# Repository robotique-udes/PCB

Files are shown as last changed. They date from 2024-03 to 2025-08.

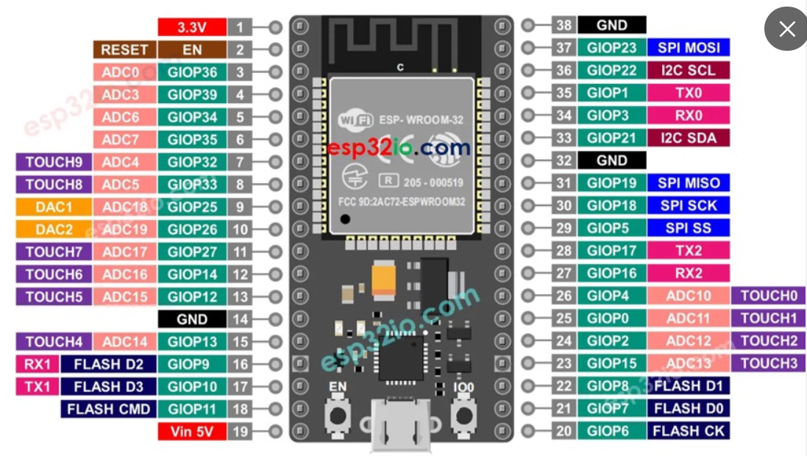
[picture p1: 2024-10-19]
exo/ACE 2024/Motherboard/ESP32_CHUNGUS_RAPIDUS/Pinout_ESP32.png

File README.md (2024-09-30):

# PCB

Cette repo regroupe les fichiers et projets de PCB de tous les sous-groupe de robotique UdeS. Chaque groupe s'organise dans son dossier. Dans le futur il serait pertinent de monter une librairie de Symbole et de Footprint globale entre les groupes.

## Protection de branches:

- Seulement les branches nommées avec ce pattern sont acceptées:
  - rover/**
  - exo/**

- Une Pull Request est requise pour pouvoir merge dans le main

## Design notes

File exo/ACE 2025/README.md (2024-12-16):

# 2025 Standard électronique
Pour la fixation des pcb, il est standardisé d'utiliser des vis M3.
Ne pas utiliser de micro vias.
## PIN Layout pour la communication en cable ethernet
Pin 1: CAN+
Pin 2: CAN-
Pin 3: SCL+
Pin 4: SCL-
Pin 5: SDA+
Pin 6: SDA-
Pin 7: 5V
Pin 8: GND

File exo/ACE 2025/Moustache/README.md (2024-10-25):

# 2025 Exo Moustache 
The Moustache is a small pcb made to receive I2C in differential, CAN and power by an ethernet port and distributed trought 6 other ethernet port to connect the captors and motors.
## PIN Layout
Pin 1: CAN+

Pin 2: CAN-

Pin 3: SCL+

Pin 4: SCL-

Pin 5: SDA+

Pin 6: SDA-

Pin 7: 5V

Pin 8: GND
## Port Layout
MOTG = moteur Genou

MOTH = moteur Hanche

BNOF = BNO Femur

BNOT = BNO Tibia

EXT = extra

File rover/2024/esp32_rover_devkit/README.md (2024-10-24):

# Antenna
PCB servant de module GPS

Voici les informations concernant le PCB : Module GPS

## Image du PCB en 3D
Capture d’écran, le 2024-09-25 à 21 09 17

## Objectifs:
* Permettre au Rover d'avoir des information sur sa position GPS

## Composants principaux:
* ESP32-S3-WROOM-1
* TJA1050T (CAN BUS)
* BN-880 (GPS)
* Ports Ethernets
* AZ1117ID-3.3 (LDO)
* TVS diodes

## Fonctionnement:
Le MCU peut lire les données du GPS.
Le MCU peut transmettre les informations du GPS par le CAN bus.
Le CAN bus peut passer à travers le circuit, donc un autre circuit peut être branché à la suite de celui-ci.

## PGIO
### Outputs

Name         | GPIO
---          | ---
LED_BUILDIN  | D2
STEPPIN      | D37
DIRPIN       | D38
ENABLEPIN    | D39

### Communication

Name    | GPIO
---     | ---
USBN    | D19
USBP    | D20
SCL     | D21
SDA     | D09
TX_GPS  s| D13
RX_GPS  | D12
TXC     | D48
RXC     | D47

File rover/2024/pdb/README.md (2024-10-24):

# PDB (Power Distribution Board)
PCB servant à gérer la distribution à bas courant et le de data du rover

## Image du PCB en 3D
Capture d’écran, le 2024-09-18 à 21 24 36

## Objectifs:
* Protéger tous les autres boards du Over/Under Voltage pour le 5V, 12V et 24V
  * Seulement le 5v et le 24v sont protégé, car les résistance 5% ont trop  d'incertitude.
* Injecteur POE(12V custom pinout) pour les cameras branché en Ethernet
  * On/Off possible par le MCU
* Diriger le signal des cameras sur les bonnes pins selon la norme Ethernet
* Agir en tant que POE pour les antennes 24V (vrai POE)
* Controller l'alimentation de 2 circuit d'accessoires 12V 
  * Par 2 connecteurs Ethernet
* Permettre de pouvoir sortir une des 3 tension (5v, 12v, 24v) par un screw terminal
  * Alimente la switch ethernet en dessous
* MCU Connecté sur le CAN BUS
* Sélectionner avec les GPIO les cameras qui doivent recevoir du power

## Composants principaux:
* ESP32 DEV KIT V1
* TJA1050 (CAN BUS)
* LTC4365 (Over/Under Voltage protaction)
* DMG4822SSD (DIODE pour la switch du LTC4365)
* DELs
* CLP6C-FKB-CKNPRGJBB7A363 (ERROR DEL)
* Boutons
* Horizontal Amphenol 54602 RJ45
* ASSMANN_A-2014 Ethernet connector
* CRJ036-5-TH_2x4 Ethernet connector
* BTS5200 (4 Channel Mosfet)

## Fonctionnement:
- Le PDB reçoit 3 tensions régulé en entrée, du 5V, du 12V et du 24V.
- Le 12V sert principalement pour alimenter les caméras qui sont alimentés avec un POE avec un Pinout spécial. Il sert aussi à alimenter 2 circuit d'accessoires potentiels.
- Le 24V sert à alimenter le/les antennes qui sont sur le Rover.
- Le 5V est passé avec les fils de CanBus pour alimenter et communiquer avec les autres PCB du rover
- Le circuit sécurise les trois tensions contre les sur-tensions et le drops de tensions.
- La sortie vers l'ordinateur principal n'est pas utilisé, l'ordinateur est directement branché dans la switch.

## PGIO
### Outputs

| Name | GPIO |
|---|---|
| CAM_SIGN_0 | D18  |
| CAM_SIGN_1 | D19  |
| CAM_SIGN_2 | D33  |
| CAM_SIGN_3 | D32  |
| PWM_0 | D21  |
| PWM_1 | D22  |
| ACC1_CONTROL | D23  |
| ACC2_CONTROL | D25  |
| LED_R | D14  |
| LED_G | D27  |
| LED_B | D26  |

### Communication

| Name | GPIO |
|---|---|
| TXC  | D6 |
| RXC  | D7 |

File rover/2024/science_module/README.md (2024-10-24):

# PCB du module science

## Image du PCB en 3D
Capture d’écran 2024-10-02 202944

## Objectifs:
* Contrôller les actionneurs du module science
  * Fan
  * Moteur DC (Grinder)
  * Actuateur linéaire
  * 4x servos
* PDB pour ces actionneurs
* Communication avec le reste du Rover

## Composants principaux:
* ESP32 S3 WROOM
* Connecteur Ethernet
* 2x bouton
* Connecteur XT60 mâle
* 6x connecteur XT30 femelle
* 2x connecteur XT30 mâle
* 8x connecteur à 2 pins
* Connecteur à 4 pins
* 6x slot à fusible
* LED

## Fonctionnement:
* Le PCB reçoit du 24V par le XT60
* Un buck down 24V -> 5V externe est connecté par deux XT30 (1 femelle, 1 mâle)
* Un buck down 24V -> 12V externe est connecté par deux XT30 (1 femelle, 1 mâle)
* Chacune des deux fans du vaccum a un connecteur XT30 à 12V
* Le grinder et l'actuateur linéaire sont chacun alimentés par un connecteurs XT30 à 24V
* LIN_IN_1 et LIN_IN_2 passent par un H-bridge et deviennet LIN+ et LIN- afin de pouvoir contrôller le sens de l'actuateur linéaire
* Les 8 connecteurs à 2 pins servent à ??????????? (Envoyer des signaux de contrôle? PB?)
* La pin 1 du ethernet est le CAN High et la pin 2 est le CAN Low

## PGIO:
### Outputs

| Name | GPIO |Commentaires |
|---|---|---|
| GRINDER_PWM  | IO10 | |
| PB_GRINDER | IO11 | |PB -> outputs ou inputs? PB-> Push Button? Connecteurs?
| FAN_B_PWM | IO3  | |
| FAN_A_PWM | IO9  | |
| PB_VACCUM | IO38 | |
| Servo_0 | IO7  | |
| Servo_1 | IO15 | |
| Servo_2 | IO16 | |
| Servo_3 | IO17 | |
| LIN_IN_1 | IO18 | Parle au H-Bridge |Outputs pour l'actuateur linéaire?
| LIN_IN_2 | IO8  | Parle au H-Bridge |
| PB_UP | IO14 | |
| PB_DOWN | IO21 | |
| PB_CAROUSSEL | IO12 | |
| PB_SPARE | IO13 | |
| LED_BUILDIN  | IO5  | |À quoi sert cette LED?

### Inputs

| Name | GPIO |Commentaires |
|---|---|---|
| EN_PB | EN | Bouton Enable |
| GPIO_0 | IO1  | Bouton Boot |
| LS_EXT | IO2  | Limit switch |
| LS_RET | IO3  | Limit switch |

### Communication

| Name | GPIO |Commentaires |
|---|---|---|
| RXC | IO47 | Parle au Ethernet (CanBus) |
| TXC | IO48 | Parle au Ethernet (CanBus) |
| USB_N | IO19 | Parle au port micro-SD |
| USB_P | IO20 | Parle au port micro-SD |

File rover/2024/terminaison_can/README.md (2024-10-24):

# Terminaison CAN bus
Petit PCB qui sert de terminaison aux extrémités du CAN bus.

## Image du PCB en 3D
Capture d’écran, le 2024-09-25 à 19 42 32

## Objectifs:
* Requis de la couche transport du CanBus:
  * 2 terminaisons de 120 ohms doivent être branchés aux extrémités du bus.
    * Sur un bus OK on doit mesurer 60 Ohms
* Agir comme un indicateur visuel de s'il y a de l'alimentation en parallèle des lignes CanBus

## Composants principaux:
* Connecteur RJ45 pour câble ethernet
* 2x Résistances 60 ohms
* Condensateur 47nF
* Résistance 2k ohms
* DEL

## Fonctionnement:
Deux résistances de 60 ohms sont placées en série entre le CAN HIGH et le CAN LOW en une résistance combinée de 120 ohms, ce qui est le standard dans une terminaison CAN. La résistance permet de dissiper le signal passant dans le bus.

Le condensateur permet de créer un filtre passe-bas qui nettoie encore plus le signal.

Il y a aussi une résistance et une diode qui sont connectées entre le VCC et le GND afin d'indiquer visuellement (par une DEL allumée) qu'il y a du courant sur les pins 7 et 8.

## Références:
* https://electronics.stackexchange.com/questions/512653/can-split-termination-capacitor-calculation
* https://www.mouser.ca/datasheet/2/302/TJA1050-3083416.pdf

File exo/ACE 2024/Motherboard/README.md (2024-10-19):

# Motherboard
Mise à jour 2024 avec un mutliplexeur embarqué pour la communication avec les 5 BNO_085. Le board est supposé être utilisé avec un ESP-WROOM-32.

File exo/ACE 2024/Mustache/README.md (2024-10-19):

# Mustache breakout board
PCB présent sur chaque jambe pour la redistribution des signaux I2C et des encodeurs. Les connecteurs sont des MOLEX disponibles dans le dossier Bibliotheque.

## Problèmes connus
- L'ajout d'une résistance pull-up avec le 3v3 à été nécessaire pour aider l'intégrité du signal I2C

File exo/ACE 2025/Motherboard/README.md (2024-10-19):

# 2025 Exo Motherboard
PCB principal sur l'exo, utilisant le SoM en socket M2 ayant un ESP-32-S3.

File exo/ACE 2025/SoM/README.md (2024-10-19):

# SoM
ESP32-S3 on a compact format with a M2 socket connecter for integration on other board.

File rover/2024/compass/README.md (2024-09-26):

# Antenna
PCB servant de module de centrale inertielle et de boussole

Voici les informations concernant le PCB : Module Compass

## Image du PCB en 3D
Capture d’écran, le 2024-09-25 à 20 08 11

## Objectifs:
* Permettre au Rover d'avoir des information sur sa position et son orientation dans l'espace
* 

## Composants principaux:
* ESP32-S3-WROOM-1
* TJA1050T (CAN BUS)
* WT901 (compass)
* Ports Ethernets
* AZ1117ID-3.3 (LDO)
* TVS diodes

## Fonctionnement:
Le MCU peut lire les données de la centrale inertielle et boussole par UART.
Le MCU peut transmettre les informations du senseur par le CAN bus.
Le CAN bus peut passer à travers le circuit, donc un autre circuit peut être branché à la suite de celui-ci.

## PGIO
### Outputs

Name         | GPIO
---          | ---
LED_BUILDIN  | D2
STEPPIN      | D37
DIRPIN       | D38
ENABLEPIN    | D39

### Communication

Name    | GPIO
---     | ---
USBN    | D19
USBP    | D20
SCL     | D21
SDA     | D09
TX_WT   | D13
RX_WT   | D12
TXC     | D48
RXC     | D47

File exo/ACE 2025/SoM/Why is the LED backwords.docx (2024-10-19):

Why is the LED backwords? It is fixed

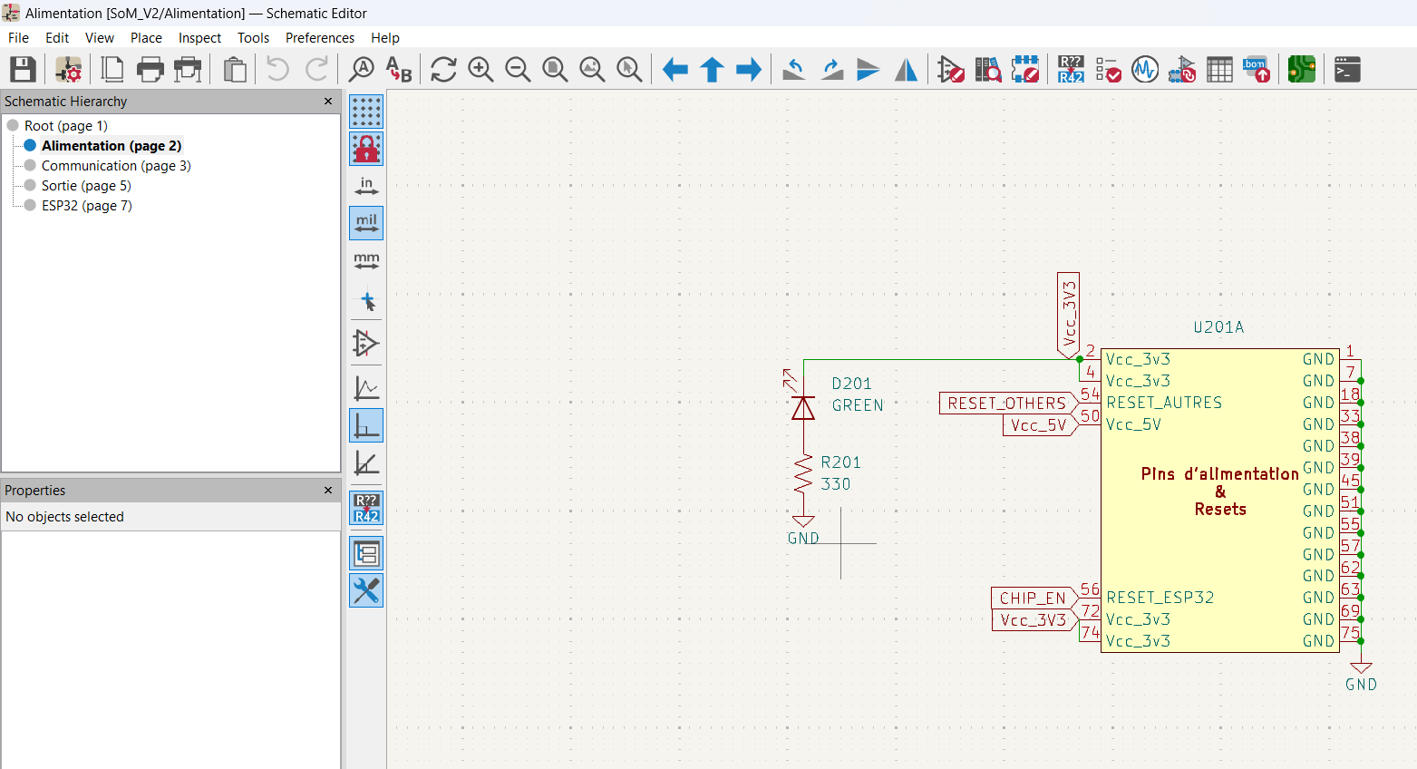
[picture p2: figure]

GND a la patte 3? Non, c Frank qui est cave, c sure que c pas un GND.

Mais le CAP(C303) me pose question? C fine

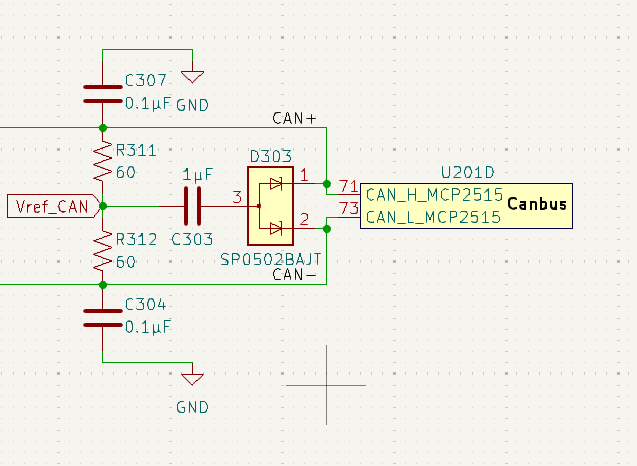
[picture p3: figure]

Will have to make sure? Should be fine

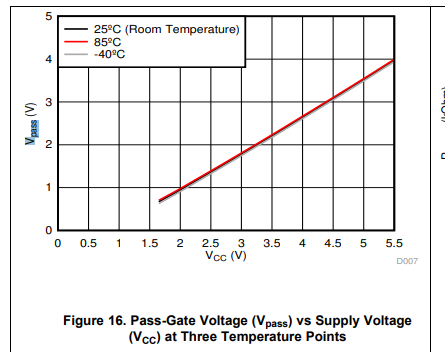
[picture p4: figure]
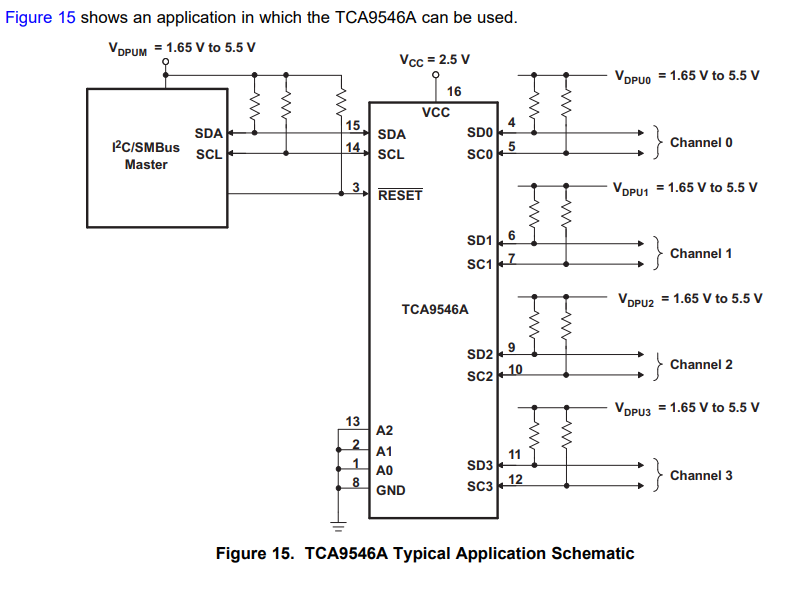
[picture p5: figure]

DS_FT231

Weird thing happening on pin 10 and 12

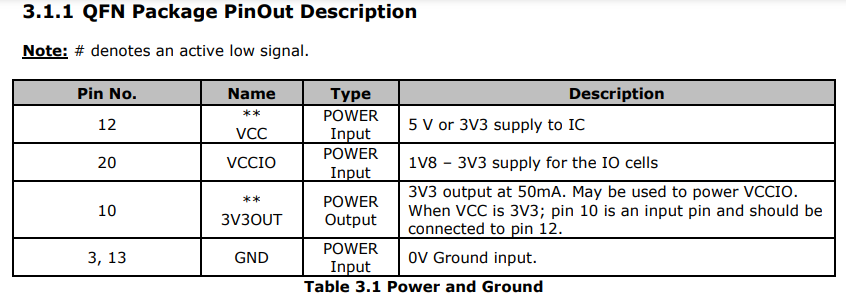
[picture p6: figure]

This is no longer used ???

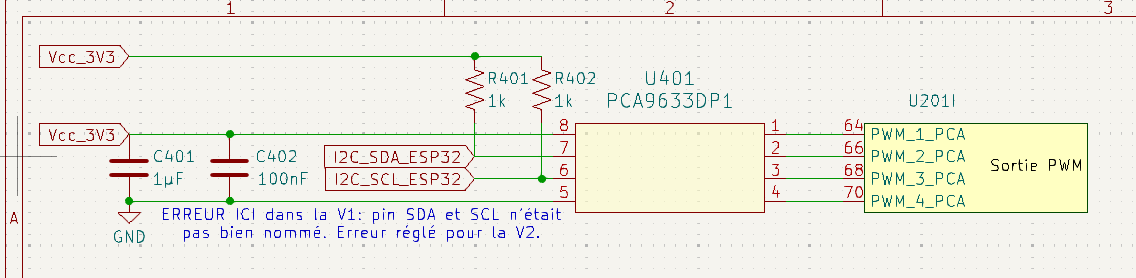
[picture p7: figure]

Good boy :

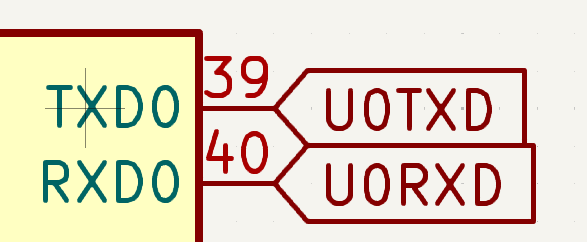
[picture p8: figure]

Mobo_V1

Why 2 of them? You could use one of them?

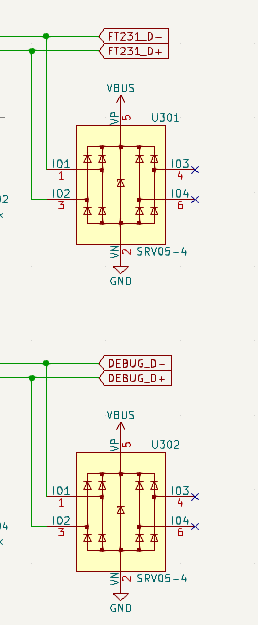
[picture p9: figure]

AMS1117-5.0

Me does not like This, with the 5V input that we have :

I will look at the mosfet later

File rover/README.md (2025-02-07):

# PCB

Ce répertoire contient les projets du rover, les projets sont trié par version du rover:

| Compétition | Surnom du rover | Nom |
|---|---|---|
| CIRC 2024 | T_REX | Teleoperated Rover for Extraterrestrial Xploration |
| CIRC 2025 | TODO | |

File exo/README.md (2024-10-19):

# PCB

Ce répertoire contient les projets de BioGenius, les projets sont trié par version du rover:

| Compétition | Nom |  Description |
|---|---|---|
| ACE 2023 | Darianne | Exo léger, 1st place ACE 2023 |
| ACE 2024 | Biggy (?) | Exo avec support a bonbonne de pompier, 3rd place |
| ACE 2025 | TBD | |

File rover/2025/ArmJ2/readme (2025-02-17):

REV0 - C'est le first draft un peu gros, mais normalement tout est chill

REV1 - Version un peu plus compacte, avec un meilleur layout des composantes (commander celui la)

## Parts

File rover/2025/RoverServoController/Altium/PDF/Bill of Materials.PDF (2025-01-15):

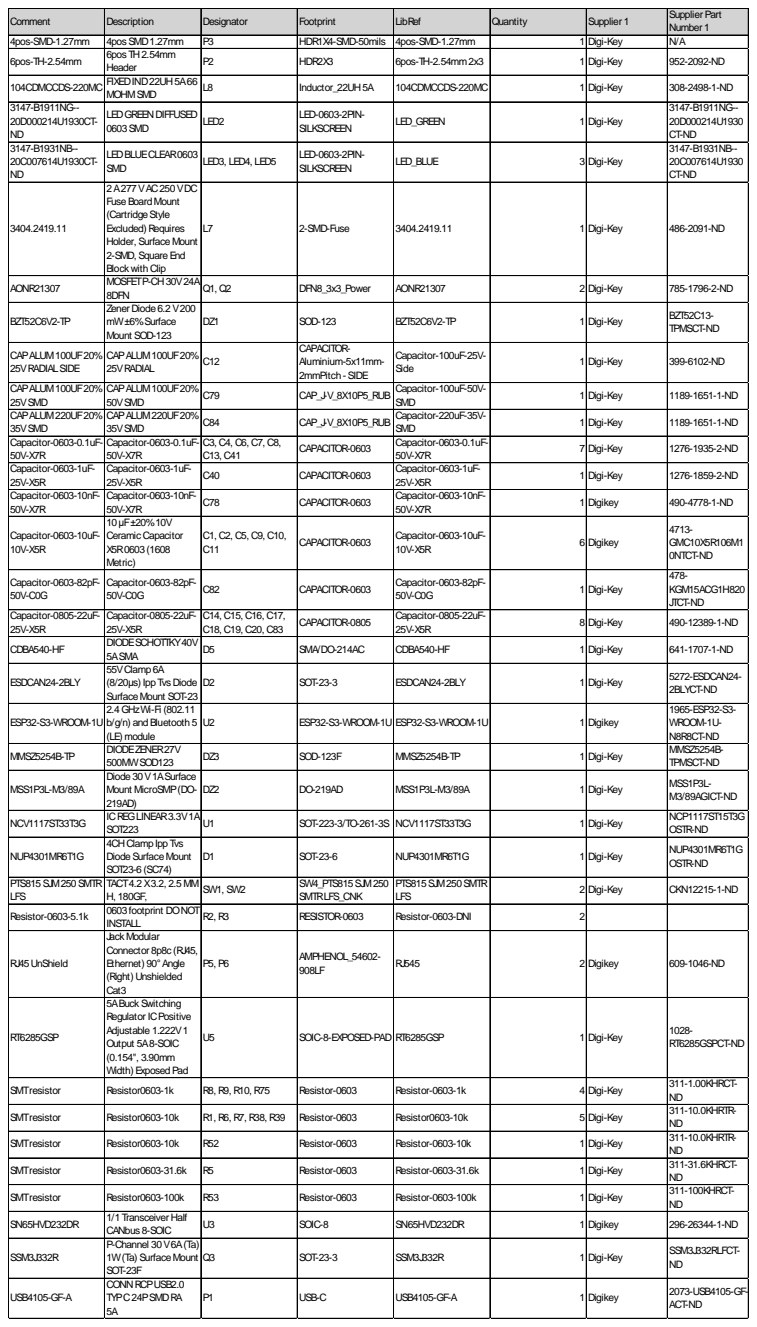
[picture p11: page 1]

Comment | Description | Designator | Footprint | LibRef | Quantity | Supplier 1 | Supplier Part Number 1

4pos-SMD-1.27mm | 4posSMD1.27mm | P3 | HDR1X4-SMD-50mils | 4pos-SMD-1.27mm | 1 | Digi-Key | N/A
6pos-TH-2.54mm | 6pos TH2.54mm Header | P2 | HDR2X3 | 6pos-TH-2.54mm2x3 | 1 | Digi-Key | 952-2092-ND

104CDMCCDS-220MC | FIXEDIND22UH5A66 MOHMSMD | L8 | Inductor_22UH5A | 104CDMCCDS-220MC | 1 | Digi-Key | 308-2498-1-ND

3147-B1911NG--20D000214U1930CT-ND | LEDGREENDIFFUSED 0603SMD | LED2 | LED-0603-2PIN-SILKSCREEN | LED_GREEN | 1 | Digi-Key | 3147-B1911NG--20D000214U1930 CT-ND

3147-B1931NB--20C007614U1930CT-ND | LEDBLUECLEAR0603 SMD | LED3, LED4, LED5 | LED-0603-2PIN-SILKSCREEN | LED_BLUE | 3 | Digi-Key | 3147-B1931NB--20C007614U1930 CT-ND

3404.2419.11 | 2A277VAC250VDC FuseBoardMount (CartridgeStyle Excluded) Requires Holder, SurfaceMount 2-SMD, SquareEnd Block withClip | L7 | 2-SMD-Fuse | 3404.2419.11 | 1 | Digi-Key | 486-2091-ND

AONR21307 | MOSFETP-CH30V24A 8DFN | Q1, Q2 | DFN8_3x3_Power | AONR21307 | 2 | Digi-Key | 785-1796-2-ND

BZT52C6V2-TP | Zener Diode6.2V200 mW±6%Surface Mount SOD-123 | DZ1 | SOD-123 | BZT52C6V2-TP | 1 | Digi-Key | BZT52C13-TPMSCT-ND

CAPALUM100UF20% 25VRADIALSIDE | CAPALUM100UF20% 25VRADIAL | C12 | CAPACITOR-Aluminium-5x11mm-2mmPitch- SIDE | Capacitor-100uF-25V-Side | 1 | Digi-Key | 399-6102-ND

CAPALUM100UF20% 25VSMD | CAPALUM100UF20% 50VSMD | C79 | CAP_J-V_8X10P5_RUB | Capacitor-100uF-50V-SMD | 1 | Digi-Key | 1189-1651-1-ND

CAPALUM220UF20% 35VSMD | CAPALUM220UF20% 35VSMD | C84 | CAP_J-V_8X10P5_RUB | Capacitor-220uF-35V-SMD | 1 | Digi-Key | 1189-1651-1-ND

Capacitor-0603-0.1uF-50V-X7R | Capacitor-0603-0.1uF-50V-X7R | C3, C4, C6, C7, C8, C13, C41 | CAPACITOR-0603 | Capacitor-0603-0.1uF-50V-X7R | 7 | Digi-Key | 1276-1935-2-ND

Capacitor-0603-1uF-25V-X5R | Capacitor-0603-1uF-25V-X5R | C40 | CAPACITOR-0603 | Capacitor-0603-1uF-25V-X5R | 1 | Digi-Key | 1276-1859-2-ND

Capacitor-0603-10nF-50V-X7R | Capacitor-0603-10nF-50V-X7R | C78 | CAPACITOR-0603 | Capacitor-0603-10nF-50V-X7R | 1 | Digikey | 490-4778-1-ND

Capacitor-0603-10uF-10V-X5R | 10µF±20%10V Ceramic Capacitor X5R0603(1608 Metric) | C1, C2, C5, C9, C10, C11 | CAPACITOR-0603 | Capacitor-0603-10uF-10V-X5R | 6 | Digikey | 4713-GMC10X5R106M1 0NTCT-ND

Capacitor-0603-82pF-50V-C0G | Capacitor-0603-82pF-50V-C0G | C82 | CAPACITOR-0603 | Capacitor-0603-82pF-50V-C0G | 1 | Digi-Key | 478-KGM15ACG1H820 JTCT-ND

Capacitor-0805-22uF-25V-X5R | Capacitor-0805-22uF-25V-X5R | C14, C15, C16, C17, C18, C19, C20, C83 | CAPACITOR-0805 | Capacitor-0805-22uF-25V-X5R | 8 | Digi-Key | 490-12389-1-ND

CDBA540-HF | DIODESCHOTTKY40V 5ASMA | D5 | SMA/DO-214AC | CDBA540-HF | 1 | Digi-Key | 641-1707-1-ND

ESDCAN24-2BLY | 55VClamp6A (8/20µs) IppTvs Diode SurfaceMount SOT-23 | D2 | SOT-23-3 | ESDCAN24-2BLY | 1 | Digi-Key | 5272-ESDCAN24-2BLYCT-ND

ESP32-S3-WROOM-1U | 2.4 GHzWi-Fi (802.11 b/g/n) andBluetooth5 (LE) module | U2 | ESP32-S3-WROOM-1U | ESP32-S3-WROOM-1U | 1 | Digikey | 1965-ESP32-S3-WROOM-1U-N8R8CT-ND

MMSZ5254B-TP | DIODEZENER27V 500MWSOD123 | DZ3 | SOD-123F | MMSZ5254B-TP | 1 | Digi-Key | MMSZ5254B-TPMSCT-ND

MSS1P3L-M3/89A | Diode30V1ASurface Mount MicroSMP(DO-219AD) | DZ2 | DO-219AD | MSS1P3L-M3/89A | 1 | Digi-Key | MSS1P3L-M3/89AGICT-ND

NCV1117ST33T3G | ICREGLINEAR3.3V1A SOT223 | U1 | SOT-223-3/TO-261-3S | NCV1117ST33T3G | 1 | Digi-Key | NCP1117ST15T3G OSTR-ND

NUP4301MR6T1G | 4CHClampIppTvs DiodeSurfaceMount SOT23-6(SC74) | D1 | SOT-23-6 | NUP4301MR6T1G | 1 | Digi-Key | NUP4301MR6T1G OSTR-ND

PTS815SJM250SMTR LFS | TACT4.2X3.2, 2.5 MM H, 180GF, | SW1, SW2 | SW4_PTS815SJM250 SMTRLFS_CNK | PTS815SJM250SMTR LFS | 2 | Digi-Key | CKN12215-1-ND

Resistor-0603-5.1k | 0603footprint DONOT INSTALL | R2, R3 | RESISTOR-0603 | Resistor-0603-DNI | 2

RJ45UnShield | Jack Modular Connector 8p8c (RJ45, Ethernet) 90°Angle (Right) Unshielded Cat3 | P5, P6 | AMPHENOL_54602-908LF | RJ545 | 2 | Digikey | 609-1046-ND

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

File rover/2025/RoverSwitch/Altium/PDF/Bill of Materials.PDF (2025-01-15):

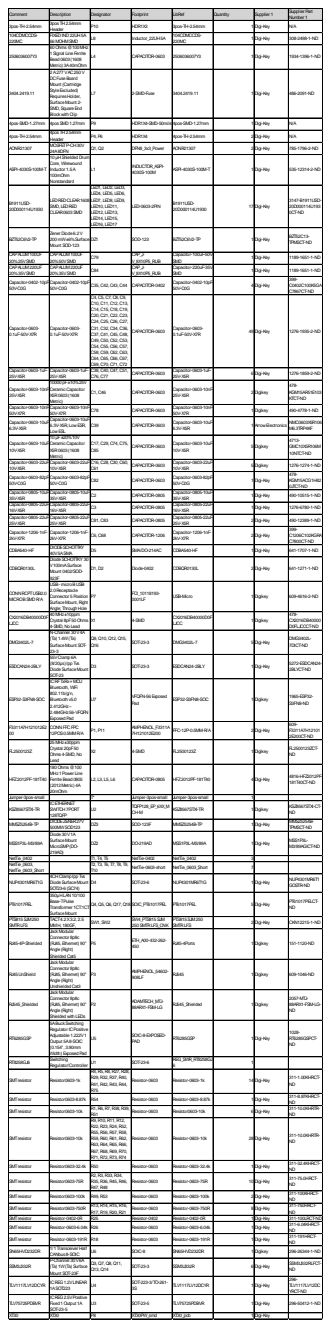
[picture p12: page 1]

Comment | Description | Designator | Footprint | LibRef | Quantity | Supplier 1 | Supplier Part Number 1

3pos-TH-2.54mm | 3posTH2.54mm Header | P10 | HDR1X3 | 3pos-TH-2.54mm | | 1 Digi-Key | N/A

104CDMCCDS-220MC | FIXEDIND22UH5A 66MOHMSMD | L8 | Inductor_22UH5A | 104CDMCCDS-220MC | | 1 Digi-Key | 308-2498-1-ND

2506036007Y3 | 60Ohms@100MHz 1Signal LineFerrite Bead0603(1608 Metric) 3A40mOhm | L4 | CAPACITOR-0603 | 2506036007Y3 | | 1 Digi-Key | 1934-1396-1-ND

3404.2419.11 | 2A277VAC250V DCFuseBoard Mount (Cartridge StyleExcluded) RequiresHolder, SurfaceMount 2-SMD,SquareEnd Blockwith Clip | L7 | 2-SMD-Fuse | 3404.2419.11 | | 1 Digi-Key | 486-2091-ND

4pos-SMD-1.27mm | 4posSMD1.27mm | P9 | HDR1X4-SMD-50mils 4pos-SMD-1.27mm | | | 1 Digi-Key | N/A

4pos-TH-2.54mm | 4posTH2.54mm Header | P4,P6 | HDR1X4 | 4pos-TH-2.54mm | | 2 Digi-Key | N/A

AONR21307 | MOSFETP-CH30V 24A8DFN | Q1, Q2 | DFN8_3x3_Power | AONR21307 | | 2 Digi-Key | 785-1796-2-ND

ASPI-4030S-100M-T | 10µHShieldedDrum Core, Wirewound Inductor 1.5A 100mOhm Nonstandard | L1 | INDUCTOR_ASPI-4030S-100M | ASPI-4030S-100M-T | | 1 Digi-Key | 535-12314-2-ND

B1911USD-20D000114U1930 | LEDREDCLEAR1608 SMD, LEDRED CLEAR0603SMD | LED1, LED2, LED3, LED4, LED5, LED6, LED7, LED8, LED9, LED10, LED11, LED12, LED13, LED14, LED15, LED16, LED17 | LED-0603-2PIN | B1911USD-20D000114U1930 | 17 Digi-Key | | 3147-B1911USD-20D000114U193 0CT-ND

BZT52C6V2-TP | Zener Diode6.2V 200mW±6%Surface Mount SOD-123 | DZ1 | SOD-123 | BZT52C6V2-TP | | 1 Digi-Key | BZT52C13-TPMSCT-ND

CAPALUM100UF 20%25VSMD | CAPALUM100UF 20%50VSMD | C79 | CAP_J-V_8X10P5_RUB | Capacitor-100uF-50V-SMD | | 1 Digi-Key | 1189-1651-1-ND

CAPALUM220UF 20%35VSMD | CAPALUM220UF 20%35VSMD | C84 | CAP_J-V_8X10P5_RUB | Capacitor-220uF-35V-SMD | | 1 Digi-Key | 1189-1651-1-ND

Capacitor-0402-10pF-50V-C0G | Capacitor-0402-10pF-50V-C0G | C35, C42, C43, C44 | CAPACITOR-0402 | Capacitor-0402-10pF-50V-C0G | | 4 Digi-Key | 399-C0402C100K5GA C7867CT-ND

Capacitor-0603-0.1uF-50V-X7R | Capacitor-0603-0.1uF-50V-X7R | C4, C5, C7, C8, C9, C10, C11, C12, C13, C14, C15, C18, C19, C20, C21, C22, C23, C24, C25, C26, C27, C31, C32, C34, C36, C37, C41, C45, C48, C49, C50, C52, C53, C54, C55, C56, C57, C58, C59, C62, C63, C64, C65, C66, C67, C69, C70, C71, C72 | CAPACITOR-0603 | Capacitor-0603-0.1uF-50V-X7R | 49 Digi-Key | | 1276-1935-2-ND

Capacitor-0603-1uF-25V-X5R | Capacitor-0603-1uF-25V-X5R | C38, C40, C47, C51, C76, C77 | CAPACITOR-0603 | Capacitor-0603-1uF-25V-X5R | | 6 Digi-Key | 1276-1859-2-ND

Capacitor-0603-10nF-25V-X5R | 10000pF±10%25V Ceramic Capacitor X5R0603(1608 Metric) | C1, C46 | CAPACITOR-0603 | Capacitor-0603-10nF-25V-X5R | | 2 Digikey | 478-KGM15AR51E103 KTCT-ND

Capacitor-0603-10nF-50V-X7R | Capacitor-0603-10nF-50V-X7R | C78 | CAPACITOR-0603 | Capacitor-0603-10nF-50V-X7R | | 1 Digikey | 490-4778-1-ND

Capacitor-0603-10uF-6.3V-X5R | Capacitor-0603-10uF-6.3V-X5R, LowESR, LowESL | C39 | CAPACITOR-0603 | Capacitor-0603-10uF-6.3V-X5R | | 1 ArrowElectronics | NMC0603X5R106 M6.3TRP4KF

Capacitor-0603-10uF-10V-X5R | 10µF±20%10V Ceramic Capacitor X5R0603(1608 Metric) | C17, C29, C74, C75, C85 | CAPACITOR-0603 | Capacitor-0603-10uF-10V-X5R | | 5 Digikey | 4713-GMC10X5R106M 10NTCT-ND

Capacitor-0603-22uF-10V-X5R | Capacitor-0603-22uF-10V-X5R | C16, C28, C30, C60, C61 | CAPACITOR-0603 | Capacitor-0603-22uF-10V-X5R | | 5 Digikey | 1276-1274-1-ND

Capacitor-0603-82pF-50V-C0G | Capacitor-0603-82pF-50V-C0G | C82 | CAPACITOR-0603 | Capacitor-0603-82pF-50V-C0G | | 1 Digi-Key | 478-KGM15ACG1H82 0JTCT-ND

Capacitor-0805-10uF-35V-X5R | Capacitor-0805-10uF-35V-X5R | C2 | CAPACITOR-0805 | Capacitor-0805-10uF-35V-X5R | | 1 Digi-Key | 490-10515-1-ND

Capacitor-0805-22uF-16V-X5R | Capacitor-0805-22uF-16V-X5R | C3 | CAPACITOR-0805 | Capacitor-0805-22uF-16V-X5R | | 1 Digi-Key | 1276-6780-1-ND

Capacitor-0805-22uF-25V-X5R | Capacitor-0805-22uF-25V-X5R | C81, C83 | CAPACITOR-0805 | Capacitor-0805-22uF-25V-X5R | | 2 Digi-Key | 490-12389-1-ND

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

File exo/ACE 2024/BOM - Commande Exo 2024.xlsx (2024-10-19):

Pour la nouvelle version de l'exo, on veut commander à nouveau tout le stock électrique pour faciliter l'installation sur l'exo et ne pas avoir à démonter l'ancien
 | Nom | QTY requise | En stock | Prix unitaire | Prix | Commentaire | Commandé | Lien
Filage
 | fil silicone 22 AWG | 1 |  | 37.45 | 37.45 | 100m | x | https://www.aliexpress.com/item/1005004583797315.html?curPageLogUid=I6X1n50ElxqA
 | fil silicone 14 AWG | 1 |  | 77.14 | 77.14 | 50m | x | https://www.aliexpress.com/item/1005004583797315.html?curPageLogUid=I6X1n50ElxqA
 | Nano fit 20-22 AWG crimp X | 600 |  | 0.1746 | 104.76 |  |  | https://www.digikey.com/en/products/detail/molex/1053002200/6131599
 | Nano fit 20-22 AWG crimp male X | 100 |  | 0.192 | 19.2 |  |  | https://www.digikey.com/en/products/detail/molex/2014472200/10257108
 | Male receptacle 4 X |  |  |  | 0 |  |  | https://www.digikey.ca/en/products/detail/molex/2014441104/10257078
 | XT30 Battery connector | 1 | 1 | 0 | 0 | On en vole à Rovus
 | 1-5 Connector |  |  |  | 0 |  |  | https://www.digikey.ca/en/products/detail/adafruit-industries-llc/5616/17506674?gad_source=1
 |  |  |  |  | 0
 |  |  |  |  | 0
 |  |  |  |  | 0
 |  |  |  |  | 0
Composants
 | Bouton d'urgence | 1 |  | 19.99 | 19.99 |  |  | https://www.amazon.ca/-/fr/mxuteuk-HB2-ES544-poussoirs-durgence-champignon/dp/B07R9QTBG7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
 | Boitier Fuse | 1 | 0 | 13.49 | 13.49 |  |  | https://www.amazon.ca/10-Gauge-Fuse-Holder-Inline/dp/B08BWRSPY1?hvadid=581886107970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
 | Dual DC Motor Drive DBH-12V | 2 | 0 | 34.18 | 68.36 |  |  | https://www.amazon.ca/Controller-Dual-Channel-Bridge-Driver-Module/dp/B07D2948RZ
 | DC DC relais | 1 | 0 | 16.99 | 16.99 |  |  | https://www.amazon.ca/XLX-High-Power-Converter-Adjustable-Protection/dp/B081X5YX8V?cv_ct_cx=buck+down+12v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
 | 4-Channel Relay Module | 1 | 0 | 10.99 | 10.99 |  |  | https://www.amazon.ca/SainSmart-101-70-101-4-Channel-Relay-Module/dp/B0057OC5O8?s=industrial
 | BNO085 | 8 | 5 | 35.99 | 287.92 |  |  | https://www.digikey.ca/en/products/detail/adafruit-industries-llc/4754/13426653
 | 3-Channel Distance Sensor | 4 | 1 | 39.95 | 159.8 |  |  | https://www.pololu.com/product/3412
 | Molex crimping tool | 1 | 0 | 26.99 | 26.99 |  |  | https://www.amazon.ca/IWISS-Crimping-Computer-Automotive-Metri-Pack/dp/B01M1YK5FM
 | Kit heat shrink | 1 |  | 18.99 | 18.99 |  |  | https://www.amazon.ca/-/fr/Assortiment-1200-gaines-thermor%C3%A9tractables-r%C3%A9tr%C3%A9cissement/dp/B0778D22WM
 | Pointe fer à souder studio | 3 |  |  | 0
 |  |  |  |  | 843.08
Molex nanofit
Endroits | Male Pin 2x2 | Male Pin 2x8 | Female 2x2 | Female 1x6 | Female 1x7 | Female 2x4 | Female 2x5 | Female 2x8 | PCB mount 2x4 | PCB mount 1x6 | PCB mount 1x7 | PCB mount 2x5 | PCB mount 2x8
Distance sensor X |  |  |  |  | 2 X |  |  |  |  |  | 2 X
PCB BNO 085 x |  |  |  |  |  | 5x |  |  | 5X
Fils Encodeurs X | 4X |  | 4X
Connexion Hanche x |  | 2X |  |  |  |  |  | 2X
Drive moteur x |  |  |  |  |  |  | 2X |  |  |  |  | 2X
Relais solenoide x |  |  |  | 1X |  |  |  |  |  | 1X
PCB Relais x |  |  |  |  |  |  |  | 2X | 8X |  |  |  | 2X
Main PCB x |  |  |  |  |  | 8x
 |  |  |  |  |  | 4x | 2x | 2X | 4 X |  |  | 2X | 2X

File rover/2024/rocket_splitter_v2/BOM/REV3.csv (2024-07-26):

Reference | Value | Datasheet | Footprint | Qty | DNP
C1 | XT60PW-M |  | Connector_AMASS:AMASS_XT60PW-M_1x02_P7.20mm_Horizontal | 1
C2,C3 | XT60PW-F |  | Connector_AMASS:AMASS_XT60PW-F_1x02_P7.20mm_Horizontal | 2
D_IN_1 | RJ45 | ~ | 54601-908WPLF:AMPHENOL_54601-908WPLF | 1 | 2
D_OUT_1,D_OUT_2 | RJ45 | ~ | 54601-908WPLF:AMPHENOL_54601-908WPLF | 2 | 4
F1,F2 | 3550 x2 | 3550-2 | footprints:3550-2_KEY | 2 | 16

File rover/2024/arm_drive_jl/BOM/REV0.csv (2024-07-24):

Reference | Value | Datasheet | Footprint | Qty | DNP
C1,C2,C7,C10,C12,C13,C15,C18 | 100nF | ~ | Capacitor_SMD:C_0805_2012Metric_Pad1.18x1.45mm_HandSolder | 8 | 16
C3 | 470uF | ~ | Capacitor_THT:CP_Radial_D8.0mm_P3.50mm | 1 | 2
C4,C5,C8,C9,C20 | 220nF | ~ | Capacitor_SMD:C_0805_2012Metric_Pad1.18x1.45mm_HandSolder | 5 | 10
C6,C11 | 1nF | ~ | Capacitor_SMD:C_0805_2012Metric_Pad1.18x1.45mm_HandSolder | 2 | 4
C14,C22 | 22uF | ~ | Capacitor_SMD:C_0805_2012Metric_Pad1.18x1.45mm_HandSolder | 2 | 4
C16 | 1uF | ~ | Capacitor_SMD:C_0805_2012Metric_Pad1.18x1.45mm_HandSolder | 1 | 2
C17,C21 | 10uF | ~ | Capacitor_SMD:C_0805_2012Metric_Pad1.18x1.45mm_HandSolder | 2 | 4
C19 | 47nF | ~ | Capacitor_SMD:C_0805_2012Metric_Pad1.18x1.45mm_HandSolder | 1 | 20
D1 | R | https://www.we-online.com/components/products/datasheet/150080SS75000.pdf | LED_SMD:LED_0805_2012Metric_Pad1.15x1.40mm_HandSolder | 1 | 2
D2 | G | https://www.we-online.com/components/products/datasheet/150080SS75000.pdf | LED_SMD:LED_0805_2012Metric_Pad1.15x1.40mm_HandSolder | 1 | 2
F1 | 10A | ~ | 3568-20:FUSE_3568-20 | 1 | 2
J1,J6 | USB_B_Micro | https://www.digikey.com/en/products/detail/amphenol-cs-fci/10118193-0001LF/2785388 | Connector_USB:USB_Micro-B_Amphenol_10118193-0001LF_Horizontal | 2 | 4
J2 | ~ | ~ | Connector_JST:JST_XH_B6B-XH-A_1x06_P2.50mm_Vertical | 1 | 0
J3 | RJ45 | ~ | A-2014-2-4-N-T-R:ASSMANN_A-2014-2-4-N-T-R | 1 | 2
J4 | XT30PW-M |  | Connector_AMASS:AMASS_XT60-M_1x02_P7.20mm_Vertical | 1 | 0
J5 | XT30PW-F | ~ | Connector_AMASS:AMASS_XT30PW-F_1x02_P2.50mm_Horizontal | 1 | 0
J7,J8 | B2B-XH-A_LF__SN_ | http://www.jst-mfg.com/product/pdf/eng/eXH.pdf | Connector_JST:JST_XH_B2B-XH-A_1x02_P2.50mm_Vertical | 2 | 4
JP1 | Jumper_3_Open | ~ | Connector_PinHeader_2.54mm:PinHeader_1x03_P2.54mm_Vertical | 1 | 2
R1,R2,R5,R15 | 3.3k | ~ | Resistor_SMD:R_0805_2012Metric_Pad1.20x1.40mm_HandSolder | 4 | 8
R3,R4,R6,R7,R10 | 10k | ~ | Resistor_SMD:R_0805_2012Metric_Pad1.20x1.40mm_HandSolder | 5 | 10
R8,R9,R11,R14 | 1k | ~ | Resistor_SMD:R_0805_2012Metric_Pad1.20x1.40mm_HandSolder | 4 | 8
R12,R13 | 60 | ~ | Resistor_SMD:R_0805_2012Metric_Pad1.20x1.40mm_HandSolder | 2 | 4
SW1,SW2,SW3,SW4 | TS09-63-25-WT-160-SMT-TR | TS09-63-25-WT-160-SMT-TR | TS09_63_25_WT_160_SMT_TR:SW_TS09-63-25_CUD | 4 | 8
U1,U2 | IFX007T | ~ | footprints:PG-TO263-7-1_INF-M | 2 | 4
U3 | 150-SMDB03CE3/TR7TR-ND | 150-SMDB03CE3/TR7TR-ND | Package_SO:SOIC-8-1EP_3.9x4.9mm_P1.27mm_EP2.29x3mm | 1 | 2
U4 | ESP32-S3-WROOM-1 | https://www.espressif.com/sites/default/files/documentation/esp32-s3-wroom-1_wroom-1u_datasheet_en.pdf | RF_Module:ESP32-S3-WROOM-1 | 1 | 2
U5 | SN65HVD232Q |  | TJA1050T_CM_118:SOIC127P600X175-8N | 1 | 2
U6 | LM7805MPX/NOPB |  | Package_TO_SOT_SMD:SOT-223-3_TabPin2 | 1 | 2
U7 | AZ1117CH-3.3TRG1 |  | Package_TO_SOT_SMD:SOT-223-3_TabPin2 | 1 | 2

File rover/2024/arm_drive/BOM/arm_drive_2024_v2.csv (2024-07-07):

Reference | Value | Datasheet | Footprint | Qty | CART
C1,C3,C4,C7,C10,C11,C17,C19,C21 | 100nF | ~ | Capacitor_SMD:C_0805_2012Metric_Pad1.18x1.45mm_HandSolder | 9 | 18
C2,C22 | 10uF | ~ | Capacitor_SMD:C_0805_2012Metric_Pad1.18x1.45mm_HandSolder | 2 | 4
C5,C9,C12,C13,C14 | 220nF | ~ | Capacitor_SMD:C_0805_2012Metric_Pad1.18x1.45mm_HandSolder | 5 | 10
C6,C23 | 22uF | ~ | Capacitor_SMD:C_0805_2012Metric_Pad1.18x1.45mm_HandSolder | 2 | 4
C8 | 1uF | ~ | Capacitor_SMD:C_0805_2012Metric_Pad1.18x1.45mm_HandSolder | 1 | 2
C15,C20 | 470uF | ~ | Capacitor_THT:CP_Radial_D8.0mm_P3.50mm | 2 | 4
C16,C18 | 1nF | ~ | Capacitor_SMD:C_0805_2012Metric_Pad1.18x1.45mm_HandSolder | 2 | 4
D1 | R | https://www.we-online.com/components/products/datasheet/150080SS75000.pdf | LED_SMD:LED_0805_2012Metric_Pad1.15x1.40mm_HandSolder | 1 | 2
D2 | G | https://www.we-online.com/components/products/datasheet/150080SS75000.pdf | LED_SMD:LED_0805_2012Metric_Pad1.15x1.40mm_HandSolder | 1 | 2
F1 | 25A | ~ | 3568-20:FUSE_3568-20 | 1 | 2
F2 | 20A | ~ | 3568-20:FUSE_3568-20 | 1 | 2
F3 | 4A | ~ | 3568-20:FUSE_3568-20 | 1 | 2
J1 | RJ45 | ~ | A-2014-2-4-N-T-R:ASSMANN_A-2014-2-4-N-T-R | 1 | 2
J2 | USB_B_Micro | https://www.digikey.com/en/products/detail/amphenol-cs-fci/10118193-0001LF/2785388 | Connector_USB:USB_Micro-B_Amphenol_10118193-0001LF_Horizontal | 1 | 2
J3 | RJ45 | ~ | 54601-908WPLF:AMPHENOL_54601-908WPLF | 1 | 2
J6,J7 | ~ | ~ | Connector_JST:JST_XH_B6B-XH-AM_1x06_P2.50mm_Vertical | 2 | 4
J9,J10 | XT30PW-F | ~ | Connector_AMASS:AMASS_XT30PW-F_1x02_P2.50mm_Horizontal | 2 | 0
R1,R2,R10,R13 | 1k | ~ | Resistor_SMD:R_0805_2012Metric_Pad1.20x1.40mm_HandSolder | 4 | 8
R3,R7,R9,R11,R12 | 10k | ~ | Resistor_SMD:R_0805_2012Metric_Pad1.20x1.40mm_HandSolder | 5 | 10
R4,R5,R6,R14,R15 | 3.3k | ~ | Resistor_SMD:R_0805_2012Metric_Pad1.20x1.40mm_HandSolder | 5 | 10
SW1,SW2,SW3,SW4,SW5,SW6,SW7 | TS09-63-25-WT-160-SMT-TR | TS09-63-25-WT-160-SMT-TR | TS09_63_25_WT_160_SMT_TR:SW_TS09-63-25_CUD | 7 | 14
U1 | 150-SMDB03CE3/TR7TR-ND | 150-SMDB03CE3/TR7TR-ND | Package_SO:SOIC-8-1EP_3.9x4.9mm_P1.27mm_EP2.29x3mm | 1 | 2
U2 | SN65HVD232Q |  | TJA1050T_CM_118:SOIC127P600X175-8N | 1 | 2
U3 | LM7805MPX/NOPB |  | Package_TO_SOT_SMD:SOT-223-3_TabPin2 | 1 | 2
U4 | DRV8251A | https://www.ti.com/lit/ds/symlink/drv8251a.pdf?ts=1647896037237 | Package_SO:Texas_HSOP-8-1EP_3.9x4.9mm_P1.27mm_ThermalVias | 1 | 2
U5 | ESP32-S3-WROOM-1 | https://www.espressif.com/sites/default/files/documentation/esp32-s3-wroom-1_wroom-1u_datasheet_en.pdf | RF_Module:ESP32-S3-WROOM-1 | 1 | 2
U6,U10 | XT60PM-M | ~ | Connector_AMASS:AMASS_XT60-M_1x02_P7.20mm_Vertical | 2 | 0
U7,U8 | BTN8962TA | ~ | footprints:PG-TO263-7-1_INF-M | 2 | 2
U9 | AZ1117CH2-3.3TRG1 |  | Package_TO_SOT_SMD:SOT-223-3_TabPin2 | 1 | 2
J0J1

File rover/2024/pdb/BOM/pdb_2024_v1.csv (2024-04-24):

Reference | Value | Datasheet | Footprint | Qty |  |  |  | PDB
C1,C4,C6 | 100nF | ~ | Capacitor_SMD:C_0805_2012Metric_Pad1.18x1.45mm_HandSolder | 3 | 3 | KGM21NR71H104KT
C2,C3,C5 | 10uF | ~ | Capacitor_SMD:C_0805_2012Metric_Pad1.18x1.45mm_HandSolder | 3 | 3 | 490-18664-1-ND
C7,C8,C9 | 100uF | ~ | Capacitor_THT:CP_Radial_D5.0mm_P2.00mm | 3 | 3 | 732-8737-1-ND
D1 | B | ~ | LED_SMD:LED_0805_2012Metric_Pad1.15x1.40mm_HandSolder | 1 | 1 | 732-4982-1-ND
D2,D5,D6,D7,D8 | Y | ~ | LED_SMD:LED_0805_2012Metric_Pad1.15x1.40mm_HandSolder | 5 | 5 | 732-4987-2-ND
D3 | R | ~ | LED_SMD:LED_0805_2012Metric_Pad1.15x1.40mm_HandSolder | 1 | 1 | 732-4984-2-ND
D4 | CLP6C-FKB-CKNPRGJBB7A363 | CLP6C-FKB-CKNPRGJBB7A363 | footprints:CLP6C-FKB-CKNPRGJBB7A363_CRE-M | 1 | 1 | CLP6C-FKB-CKNPRGJBB7A363
D10,D11 | G | ~ | LED_SMD:LED_0805_2012Metric_Pad1.15x1.40mm_HandSolder | 2 | 2 | 732-4983-2-ND
E_5V_1,E_5V_2,E_5V_3,E_5V_4 | RJ45 | ~ | 54601-908WPLF:AMPHENOL_54601-908WPLF | 4 | 6 | 609-5081-ND
E_12V_1 | RJ45 | ~ | A-2014-2-4-N-T-R:ASSMANN_A-2014-2-4-N-T-R | 1 | 5 | A-2014-2-4-N-T-R
E_12V_2 | RJ45 | ~ | 54601-908WPLF:AMPHENOL_54601-908WPLF | 1 | 0 | 609-5081-ND
E_24V_POE_IN_1 | RJ45 | ~ | A-2014-2-4-N-T-R:ASSMANN_A-2014-2-4-N-T-R | 1 | 0 | A-2014-2-4-N-T-R
E_24V_POE_IN_2 | RJ45 | ~ | 54601-908WPLF:AMPHENOL_54601-908WPLF | 1 | 0 | 609-5081-ND
E_24V_POE_OUT_1,E_24V_POE_OUT_2 | RJ45 | ~ | A-2014-2-4-N-T-R:ASSMANN_A-2014-2-4-N-T-R | 2 | 0 | A-2014-2-4-N-T-R
F1,F2 | Fuse | ~ | 3568-20:FUSE_3568-20 | 2 | 2 | 36-3568-20-ND
J1 | Screw_Terminal_01x04 | ~ | 1790335:PHOENIX_1790335_4pin | 1 | 8 | 277-6414-ND
J2,J3 | Screw_Terminal_01x02 | ~ | 1790335:PHOENIX_1790335_2pin | 2 | 0 | 277-6414-ND
JP1,JP2,JP3,JP4,JP5,JP6 | Jumper_2_Open | ~ | Connector_PinHeader_2.54mm:PinHeader_1x02_P2.54mm_Vertical | 6 | 6 | 732-5315-ND | Pas oublier jumper!
Q1,Q2 | GSF2302 | https://www.digikey.ca/en/products/detail/good-ark-semiconductor/SSF2302/21275290 | Package_TO_SOT_SMD:SOT-23_Handsoldering | 2 | 2 | 4786-SSF2302TR-ND
R1,R2,R3,R4,R5,R6,R7,R8,R9,R10,R16,R17,R18,R19,R20,R26,R27 | 10k | ~ | Resistor_SMD:R_0805_2012Metric_Pad1.20x1.40mm_HandSolder | 17 |  | 311-10.0KCRTR-ND
R11,R12,R13,R14,R15 | 0 | ~ | Resistor_SMD:R_0805_2012Metric_Pad1.20x1.40mm_HandSolder | 5 | 5 | ERJ-6GEY0R00V
R21 | 1k | ~ | Resistor_SMD:R_0805_2012Metric_Pad1.20x1.40mm_HandSolder | 1 | 1 | 4988-NRC10J102TRFTR-ND
R22,R23,R24,R25 | 47k | ~ | Resistor_SMD:R_0805_2012Metric_Pad1.20x1.40mm_HandSolder | 4 | 4 | RMCF0805JT47K0TR-ND
R28 | 68 | ~ | Resistor_SMD:R_0805_2012Metric_Pad1.20x1.40mm_HandSolder | 1 | 1 | 311-68ARTR-ND
R29,R32,R36,R40 | 100k | ~ | Resistor_SMD:R_0805_2012Metric_Pad1.20x1.40mm_HandSolder | 4 | 4 | 311-100KCRTR-ND
R30 | 1.8M | ~ | Resistor_SMD:R_0805_2012Metric_Pad1.20x1.40mm_HandSolder | 1 | 1 | 311-1.80MCRTR-ND
R31 | 200k | ~ | Resistor_SMD:R_0805_2012Metric_Pad1.20x1.40mm_HandSolder | 1 | 1 | RMCF0805FT200KTR-ND
R33 | 6.2M | ~ | Resistor_SMD:R_0805_2012Metric_Pad1.20x1.40mm_HandSolder | 1 | 1 | 541-6.20MCCT-ND
R34 | 240k | ~ | Resistor_SMD:R_0805_2012Metric_Pad1.20x1.40mm_HandSolder | 1 | 1 | 311-240KCRCT-ND
R35 | 62k | ~ | Resistor_SMD:R_0805_2012Metric_Pad1.20x1.40mm_HandSolder | 1 | 1 | 311-62KARTR-ND
R37 | 13M | ~ | Resistor_SMD:R_0805_2012Metric_Pad1.20x1.40mm_HandSolder | 1 | 1 | 13-RC0805JR-0713MLTR-ND
R38 | 270k | ~ | Resistor_SMD:R_0805_2012Metric_Pad1.20x1.40mm_HandSolder | 1 | 1 | A126354CT-ND
R39 | 30k | ~ | Resistor_SMD:R_0805_2012Metric_Pad1.20x1.40mm_HandSolder | 1 | 1 | RMCF0805FT30K0TR-ND
U1 | ~ |  | Package_SO:SOIC-14_3.9x8.7mm_P1.27mm | 1 | 1 | BTS52004EKAXUMA1CT-ND
U2 | ~ |  | ESP32-DEVKIT-V1:MODULE_ESP32_DEVKIT_V1 | 1 | 1 | 1965-ESP32-S3-WROOM-1U-N8CT-ND
U3 | TJA1050T_CM_118 |  | TJA1050T_CM_118:SOIC127P600X175-8N | 1 | 1 | 568-10292-1-ND
U4,U6,U8 | ~ | 505-LTC4365CTS8#TRMPBFTR-ND | Package_TO_SOT_SMD:TSOT-23-8_HandSoldering | 3 | 3 | 505-LTC4365CTS8#TRMPBFTR-ND
U5,U7,U9 | ~ |  | Custom:SOIC-8-1EP_3.9x4.9mm_P1.27mm_hand_solder | 3 | 3 | DMG4822SSD-13DICT-ND
U10 | ~ |  | CRJ036-5-TH:CUI_CRJ036-5-TH | 1 | 1 | CRJ036-5-TH

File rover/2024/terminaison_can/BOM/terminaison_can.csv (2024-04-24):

Reference | Value | Datasheet | Footprint | Qty | Qty Ordered |  | Header | TC
C2,C3 | 47nF | ~ | Capacitor_SMD:C_0805_2012Metric_Pad1.18x1.45mm_HandSolder | 2 |  | 1276-1250-1-ND
CON1 | ~ | https://www.farnell.com/datasheets/1885653.pdf | AAA_Custom:RJ45_MALE-AJP92A8813 | 1
D1 | LED |  | LED_SMD:LED_0805_2012Metric_Pad1.15x1.40mm_HandSolder | 1 |  | 732-4984-2-ND
R1,R2,R3,R4 | 60 | ~ | Resistor_SMD:R_0805_2012Metric_Pad1.20x1.40mm_HandSolder | 4 |  | 311-62ARCT-ND
R5 | 2k | ~ | Resistor_SMD:R_0805_2012Metric_Pad1.20x1.40mm_HandSolder | 1 |  | RMCF0805FT2K00CT-ND

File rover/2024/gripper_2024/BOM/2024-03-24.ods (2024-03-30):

Reference | Value | Footprint | Description | Qty | Dans lcart
C1,C2 | 470uf | Capacitor_THT:CP_Radial_D10.0mm_P5.00mm | Polarized capacitor 478-RPF1013471M035KTR-ND | 2 | 2 | BO. Switched for A750MV477M1VAAE018
C3,C9,C11,C12 | 100nf | Capacitor_SMD:C_0805_2012Metric_Pad1.18x1.45mm_HandSolder | Unpolarized capacitor | 4 | 4
C6,C8 | 100uf | Capacitor_THT:CP_Radial_D5.0mm_P2.00mm | ESK107M025AC3AA | 2 | 2
C7,C10,C13 | 10uf | Capacitor_SMD:C_0805_2012Metric_Pad1.18x1.45mm_HandSolder | Unpolarized capacitor | 3 | 3
D1 | G | LED_SMD:LED_0805_2012Metric_Pad1.15x1.40mm_HandSolder | Light emitting diode | 150080VS75000 | 732-4986-1-ND | 1 | 1
D2,D4 | R | LED_SMD:LED_0805_2012Metric_Pad1.15x1.40mm_HandSolder | Light emitting diode | 150080VS75000 | 732-4984-2-ND | 0 | 2
D3,D5 | R | LED_SMD:LED_0805_2012Metric_Pad1.15x1.40mm_HandSolder | Light emitting diode | 150080SS75000 | 732-4984-2-ND | 0 | 2
D6 | CLP6C-FKB-CKNPRGJBB7A363 | CLP6C-FKB-CKNPRGJBB7A363:CLP6C-FKB-CKNPRGJBB7A363_CRE |  | 1 | 1
F1,F2 | 4A | Custom:3425L200_60MR | 3425L200/60MR | 2 | 2
F3 | 1.5A | Fuse:Fuse_1812_4532Metric_Pad1.30x3.40mm_HandSolder | SMD1812B075TF/33 | 1 | 1
J1 | XT30PW-M | XT30PW-M:AMASS_XT30PW-M |  | 1 | 10
J2,J3 | XT30PW-F | XT30PW-F:AMASS_XT30PW-F |  | 2 | 10
J4 | B3B-XH-A_LF__SN_ | Connector_JST:JST_XH_B3B-XH-AM_1x03_P2.50mm_Vertical | CONN HEADER VERT 3POS 2.5MM | 1 | 0
J5,J6 | RJ45 | 54601-908WPLF:AMPHENOL_54601-908WPLF | RJ connector, 8P8C (8 positions 8 connected) | 2 | 0
R1,R2,R3,R4,R5,R20,R23 | 1K | Resistor_SMD:R_0805_2012Metric_Pad1.20x1.40mm_HandSolder | Resistor | 7 | 10
R6,R8,R9,R15,R16,R17,R18,R24 | 3.3K | Resistor_SMD:R_0805_2012Metric_Pad1.20x1.40mm_HandSolder | Resistor | 8 | 10
R7 | 0.01 | Resistor_SMD:R_1206_3216Metric_Pad1.30x1.75mm_HandSolder | Resistor: 4423-VMK-R010-1.0-UTR-ND | 1 | 1
R10,R21 | 0 | Resistor_SMD:R_0805_2012Metric_Pad1.20x1.40mm_HandSolder | Resistor | 2 | 2
R19 | 68 | Resistor_SMD:R_0805_2012Metric_Pad1.20x1.40mm_HandSolder | Resistor | 1 | 1
SW1,SW2,SW3,SW4 | TS09-63-25-WT-160-SMT-TR | TS09_63_25_WT_160_SMT_TR:SW_TS09-63-25_CUD |  | 4
U1,U2 | VNH5200ASTR-E | VNH5200ASTR_E:SO_200AS-E_STM |  | 2 | 2
U3 | ~ | ESP32-DEVKIT-V1:MODULE_ESP32_DEVKIT_V1 |  | 1 | 10
U4,U5 | ~ | Connector_JST:JST_XH_B6B-XH-AM_1x06_P2.50mm_Vertical |  | 2 | 0
U6 | TJA1050T_CM_118 | TJA1050T_CM_118:SOIC127P600X175-8N |  | 1 | 1
U7 | ~ | Custom:REG_7.4V | Regulateur 7.4V, 3A, 6s. Fait par Émile Renaud (Promo 66) | 1
U8 | INA219AxD | 296-23978-2-ND | Package_SO:SOIC-8_3.9x4.9mm_P1.27mm | Zero-Drift, Bidirectional Current/Power Monitor (0-26V) With I2C Interface, SOIC-8 | 1 | 1

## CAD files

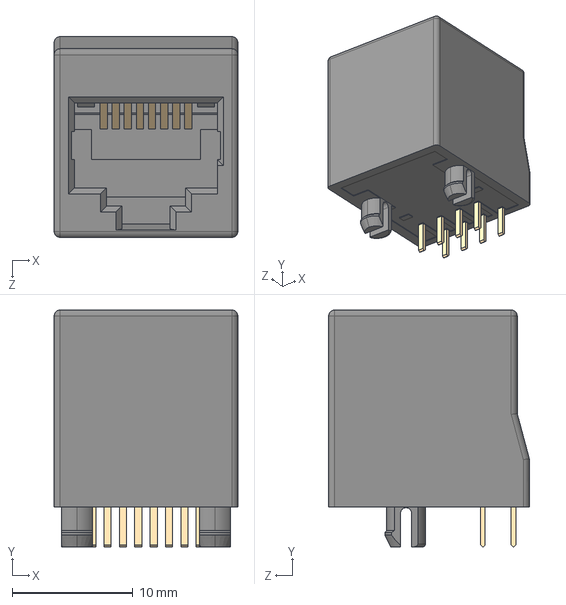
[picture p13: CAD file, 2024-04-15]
rover/2024/antenna/AntennaV1/local_lib/A-2014-2-4-N-T-R/A-2014-2-4-N-T-R.step
15.2 x 19.6 x 16.6 mm

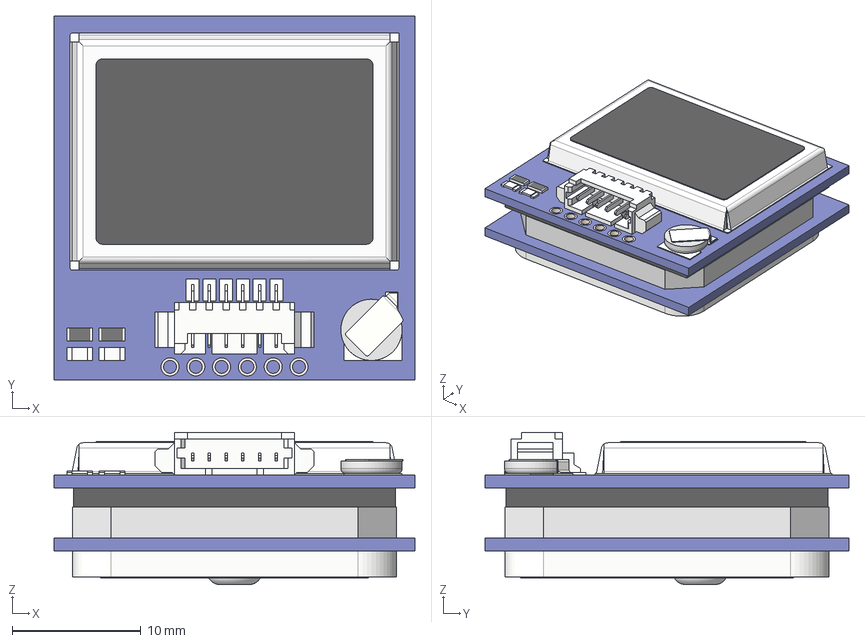
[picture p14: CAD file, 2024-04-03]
rover/2024/antenna/AntennaV1/local_lib/BN-880/Beitian BN-880 GPS and Compas.step
28.0 x 28.2 x 11.8 mm
Connector
GPS PCB
D2
D3
Pins
PPSled
PPS
Bat pad (1)
Bat pad
PPS (1)
Beitian Label
TX
Battery
GPS Shield
Solder holes
TXled
TX (1)

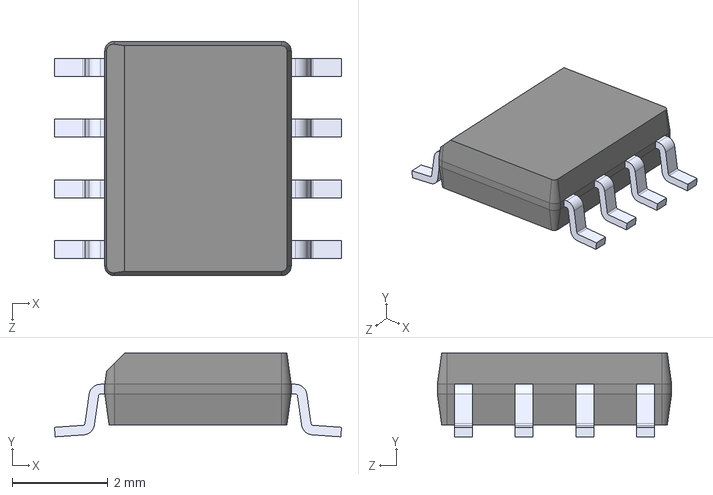
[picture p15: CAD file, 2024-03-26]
rover/2024/antenna/AntennaV1/local_lib/TJA1050T_CM_118/TJA1050T_CM_118.step
6.00 x 1.75 x 4.90 mm

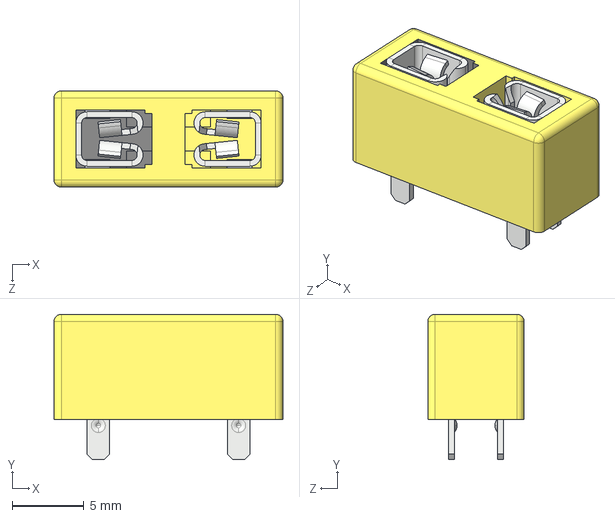
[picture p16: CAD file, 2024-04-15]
rover/2024/arm_drive/local_lib/3568-20/3568-20.step
16.0 x 10.2 x 6.73 mm

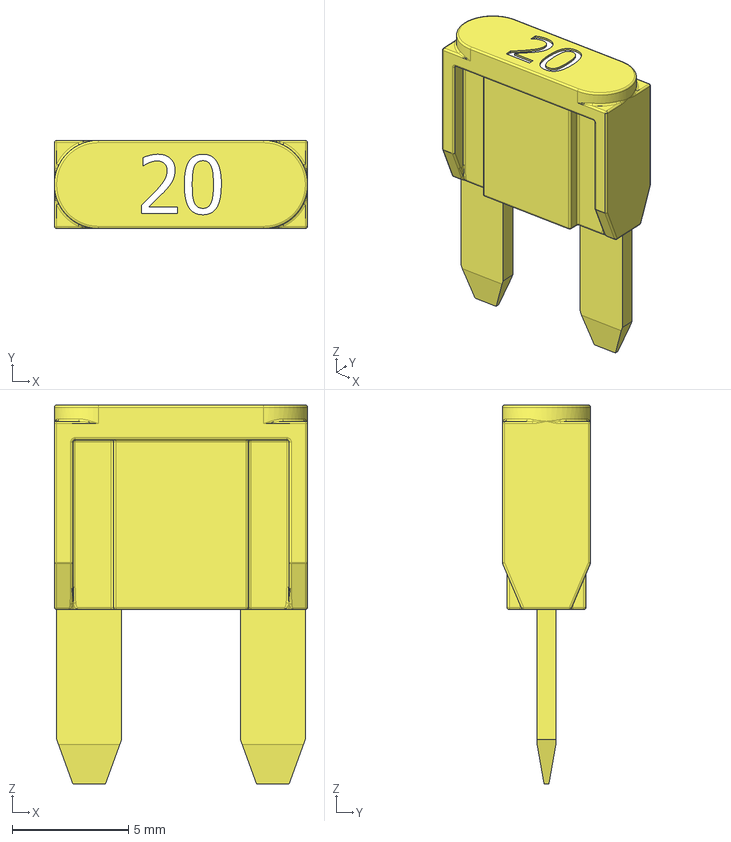
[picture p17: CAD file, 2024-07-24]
rover/2024/arm_drive_j3_4_5/local_lib/3568-20/Fusibile Lama MINI Type 2.stp
10.9 x 3.80 x 16.3 mm

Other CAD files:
rover/2024/antenna/AntennaV1/local_lib/54601-908WPLF/54601-908WPLF.step
rover/2024/antenna/AntennaV1/local_lib/Custom/Witmotion_WT901.step
rover/2024/antenna/AntennaV1/local_lib/Custom/step/JST - XH - Thru - 10Pin - 2.5mm (Genuine).stp
rover/2024/antenna/AntennaV1/local_lib/Custom/step/JST - XH - Thru - 11Pin - 2.5mm (Genuine).stp
rover/2024/antenna/AntennaV1/local_lib/Custom/step/JST - XH - Thru - 12Pin - 2.5mm (Genuine).stp
rover/2024/antenna/AntennaV1/local_lib/Custom/step/JST - XH - Thru - 13Pin - 2.5mm (Genuine).stp
rover/2024/antenna/AntennaV1/local_lib/Custom/step/JST - XH - Thru - 14Pin - 2.5mm (Genuine).stp
rover/2024/antenna/AntennaV1/local_lib/Custom/step/JST - XH - Thru - 15Pin - 2.5mm (Genuine).stp
rover/2024/antenna/AntennaV1/local_lib/Custom/step/JST - XH - Thru - 16Pin - 2.5mm (Genuine).stp
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

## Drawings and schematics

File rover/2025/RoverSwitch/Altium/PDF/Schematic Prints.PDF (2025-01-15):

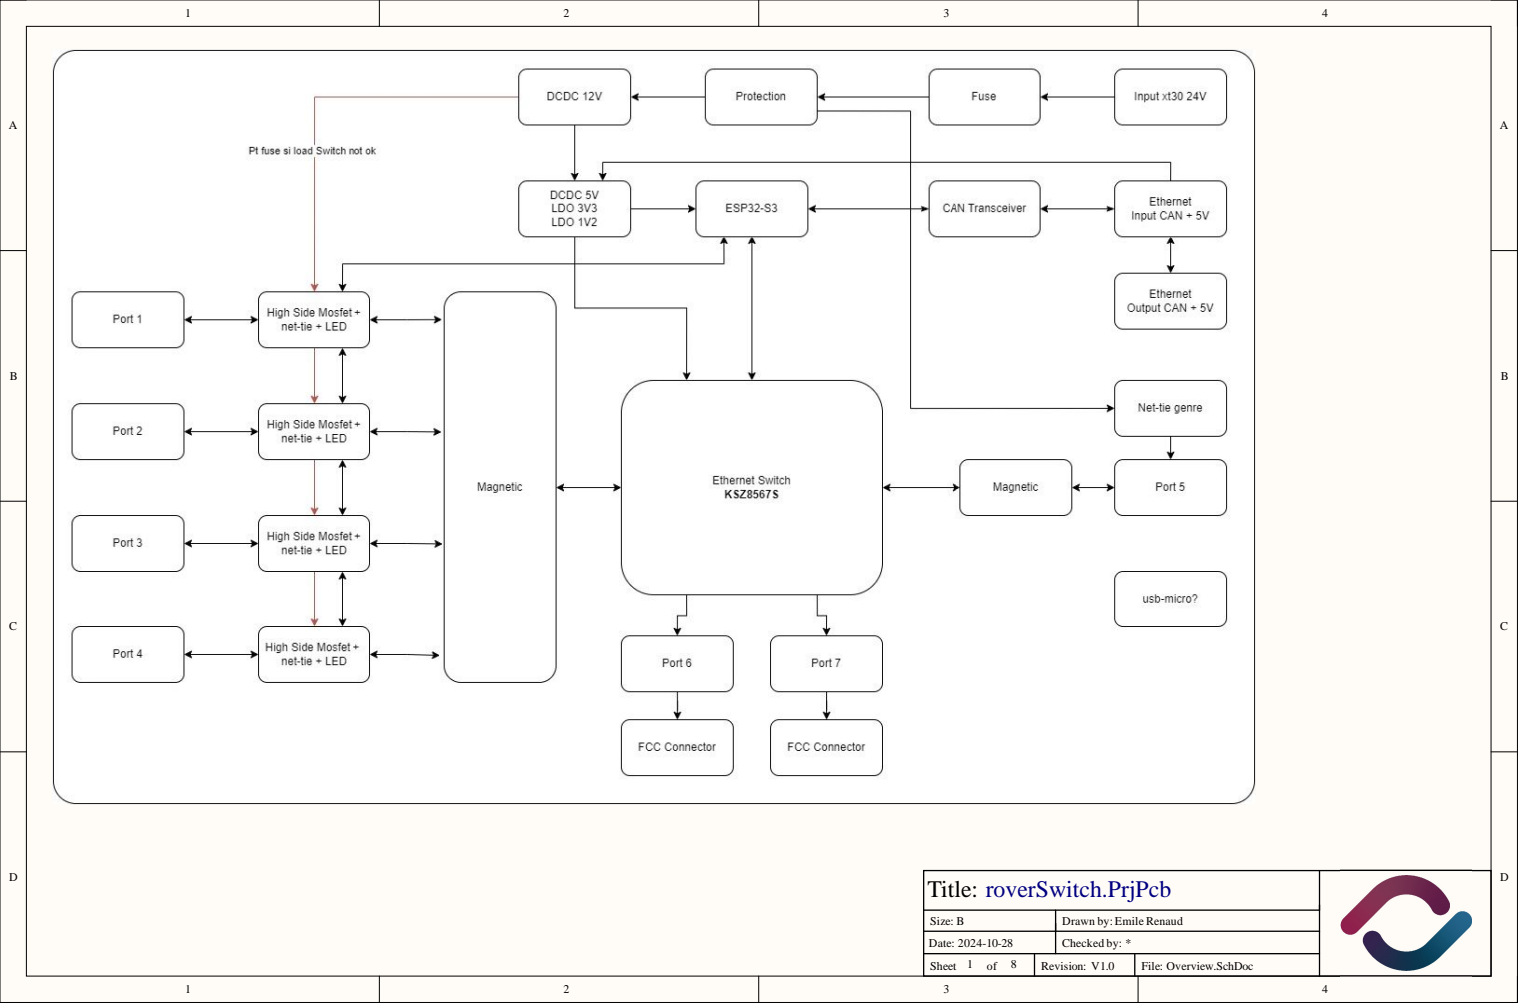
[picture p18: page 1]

Title: roverSwitch.PrjPcb

Size: B | Drawn by: Emile Renaud

Date: 2024-10-28 | Checked by: *

Sheet 1 of 8 | Revision: V1.0 | File: Overview.SchDoc

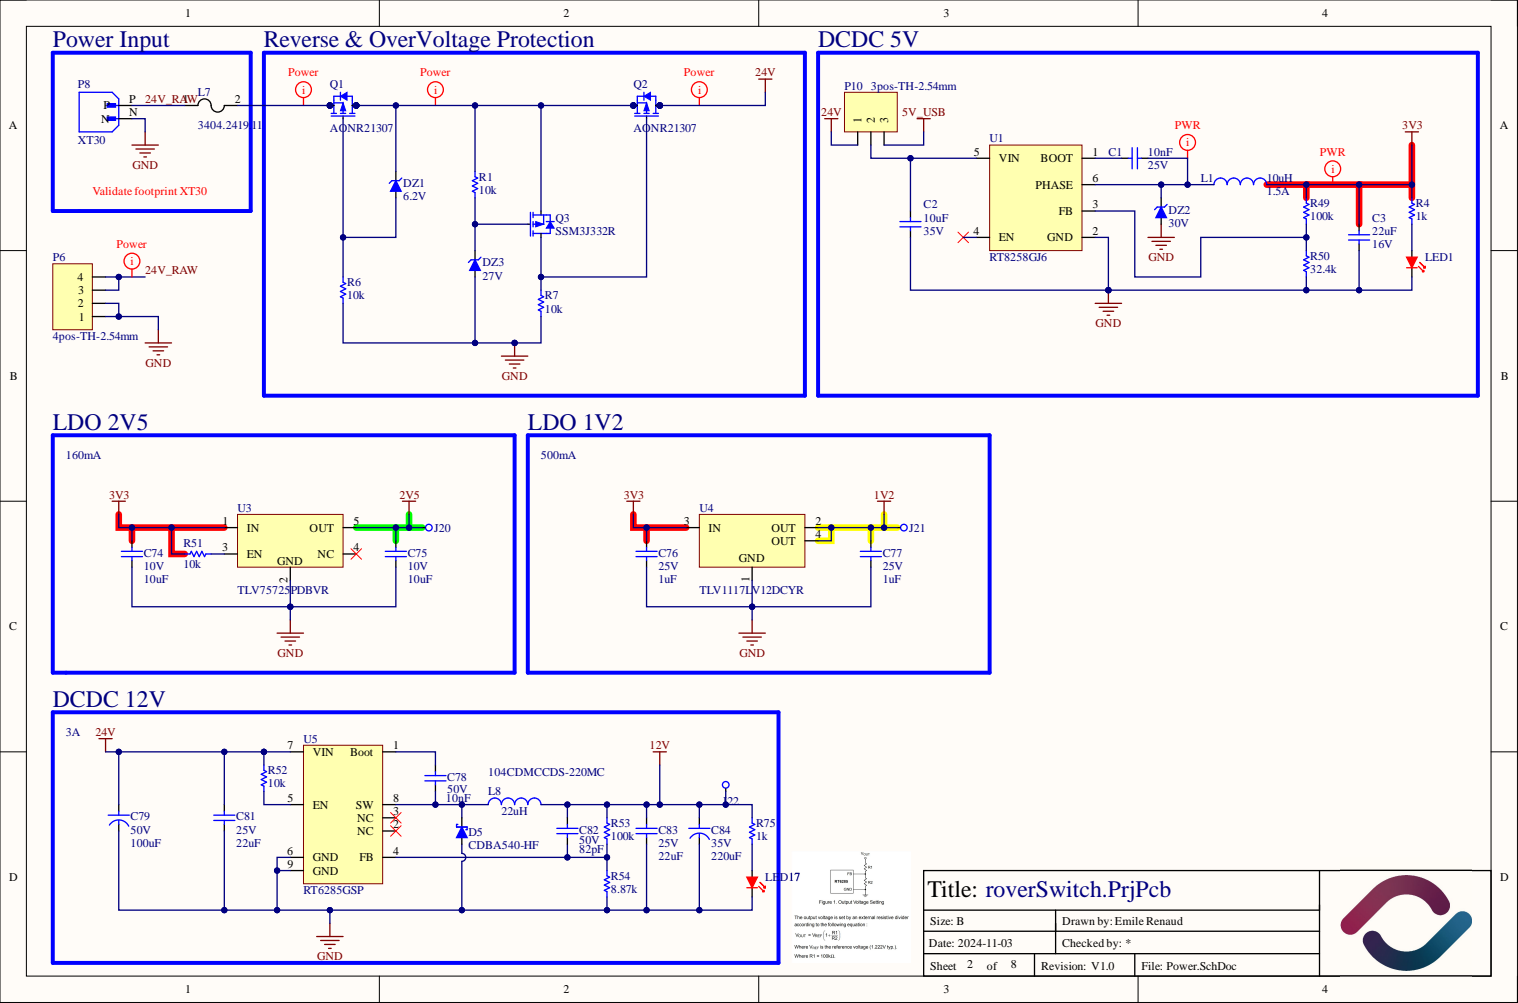
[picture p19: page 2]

Title: roverSwitch.PrjPcb

2 8 | V1.0 | Power.SchDoc

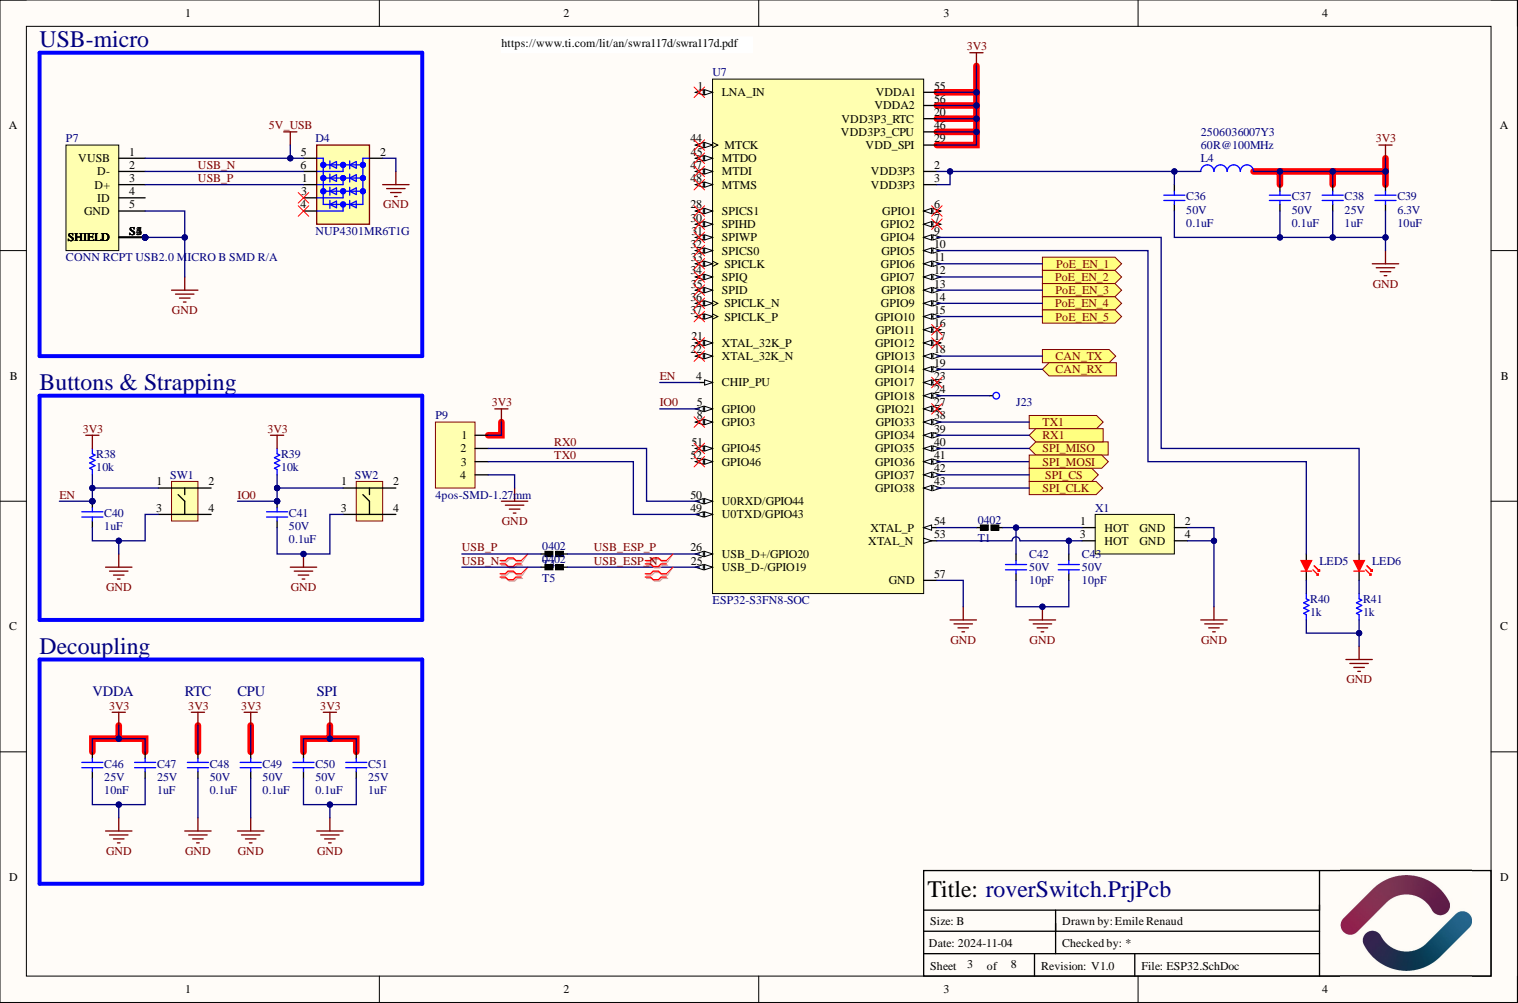
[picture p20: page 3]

https://www.ti.com/lit/an/swra117d/swra117d.pdf

CONN RCPT USB2.0 MICRO B SMD R/A

TX0 | GPIO46 52

U0RXD/GPIO44 50
U0TXD/GPIO43 49

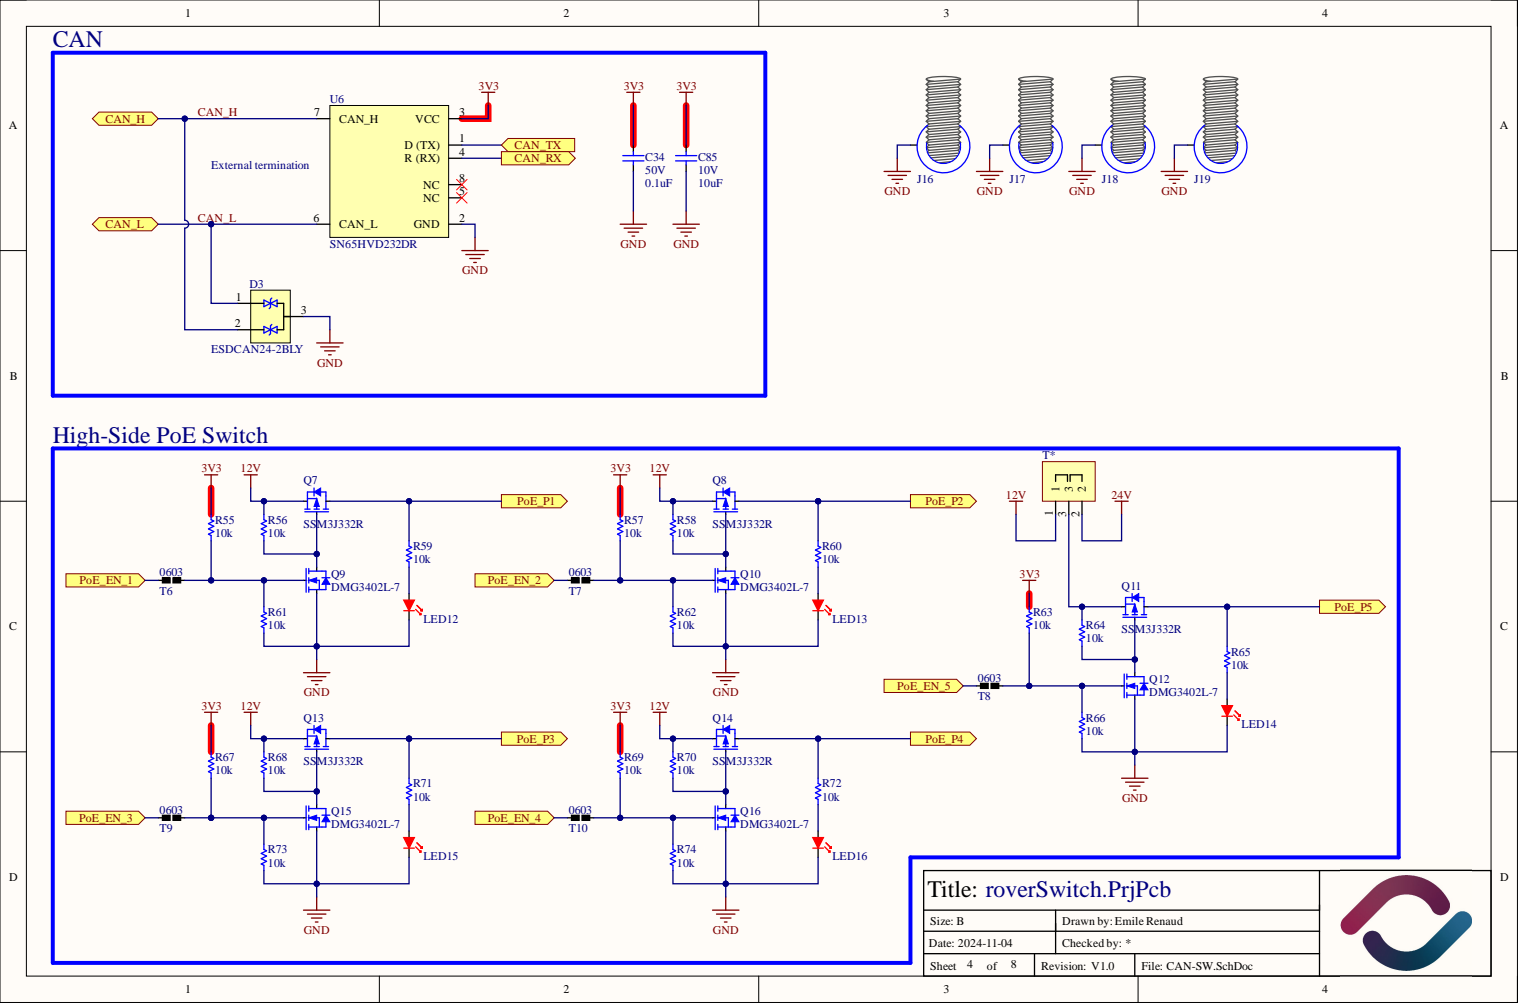
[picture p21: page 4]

High-Side PoE Switch

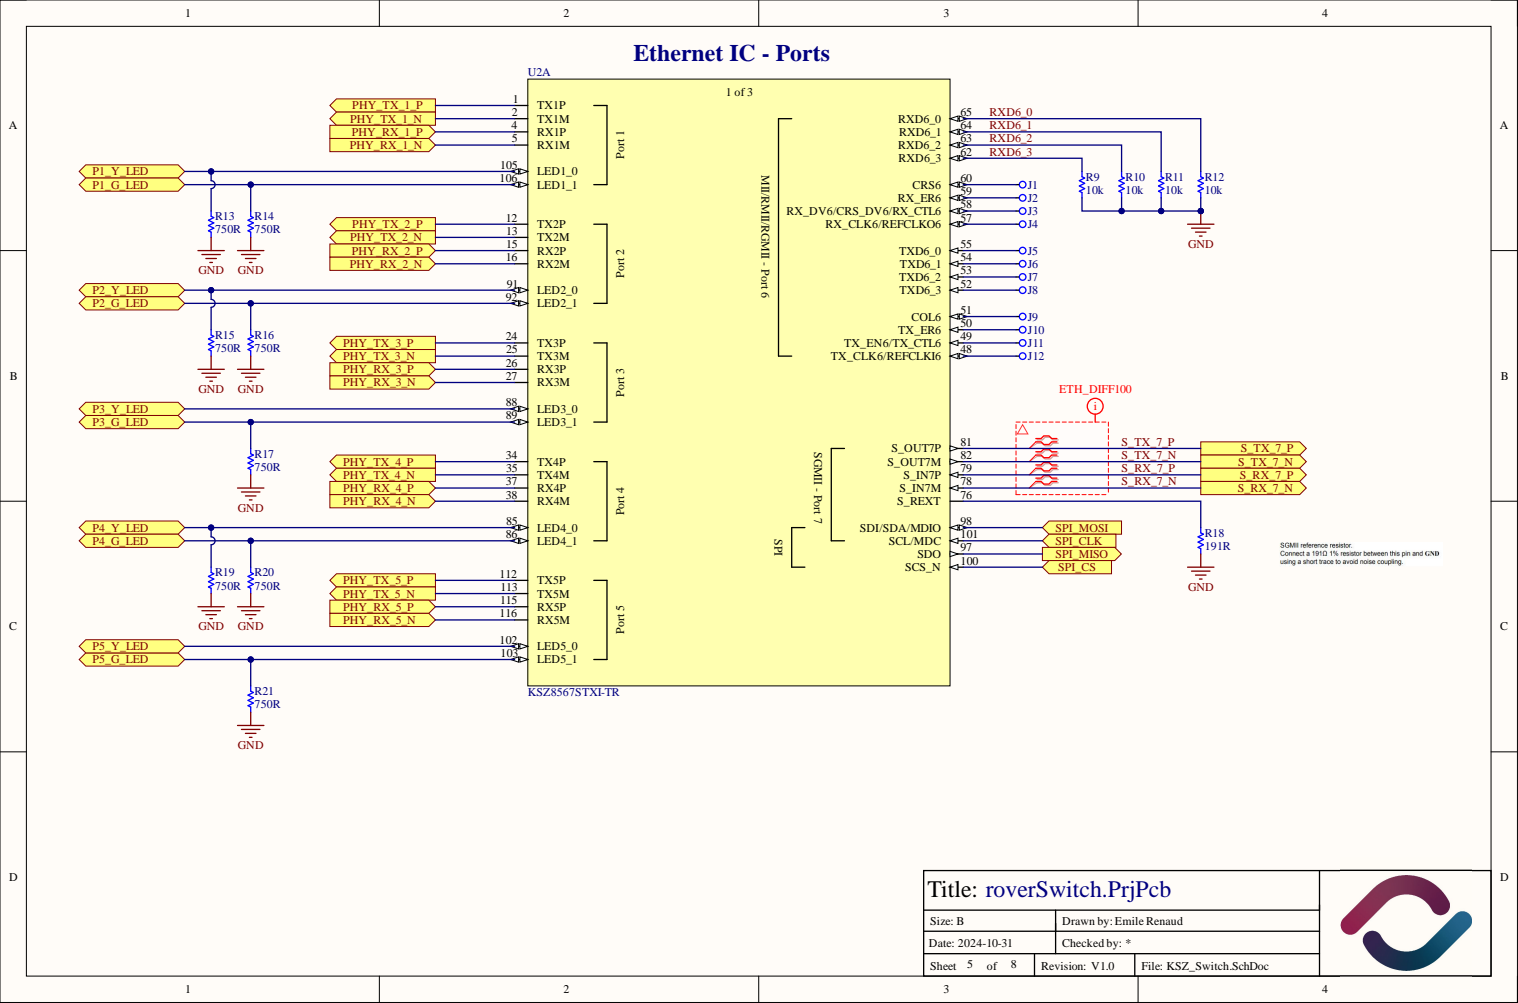
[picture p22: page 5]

RX D 6 _ 1
RX D 6 _ 2
6 RX D 6 _ 3

Port 1 Port 2 Port 3 Port 4 Port 5

MII/RMII/RGMII - Port 6

Title: B roverSwitch.PrjPcb

Size : | Draw n b y : Emi le Renau d

Dat e : 4-1 - | Checked b y : *

Shee t o f | Rev i s i o n : V . | Fi l e : KSZ _Sw i tch.Sc h D o c

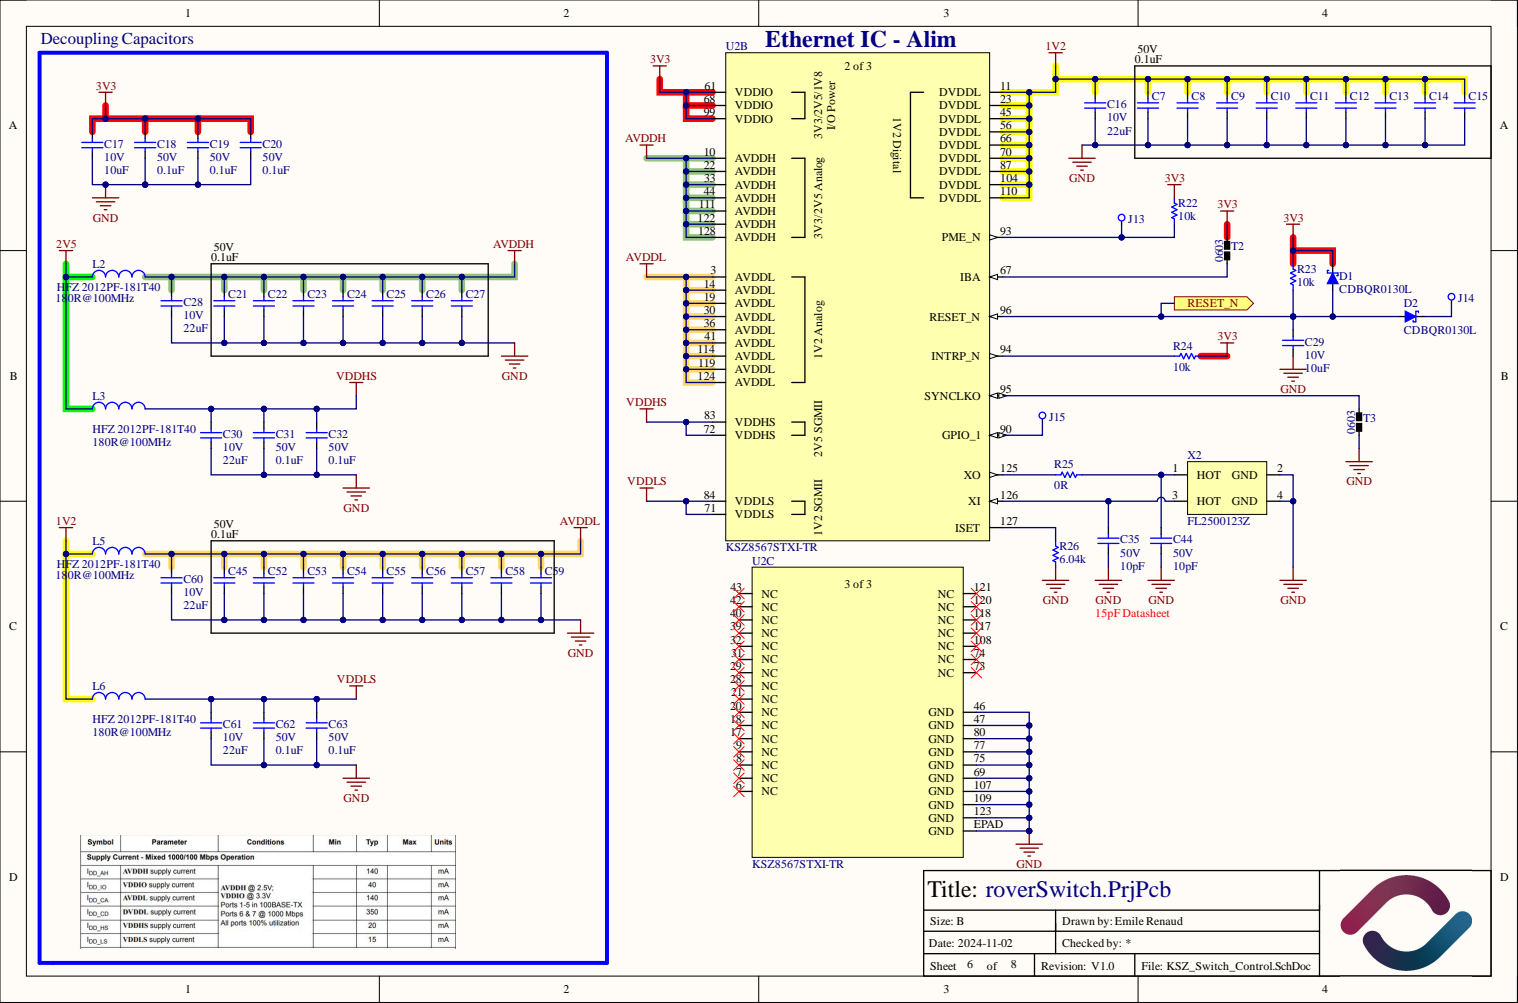
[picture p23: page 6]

AVDDH 33

AVDDH 111

AVDDL 19
AVDDL 30
AVDDL 36
AVDDL 41
AVDDL 114

AVDDL 124

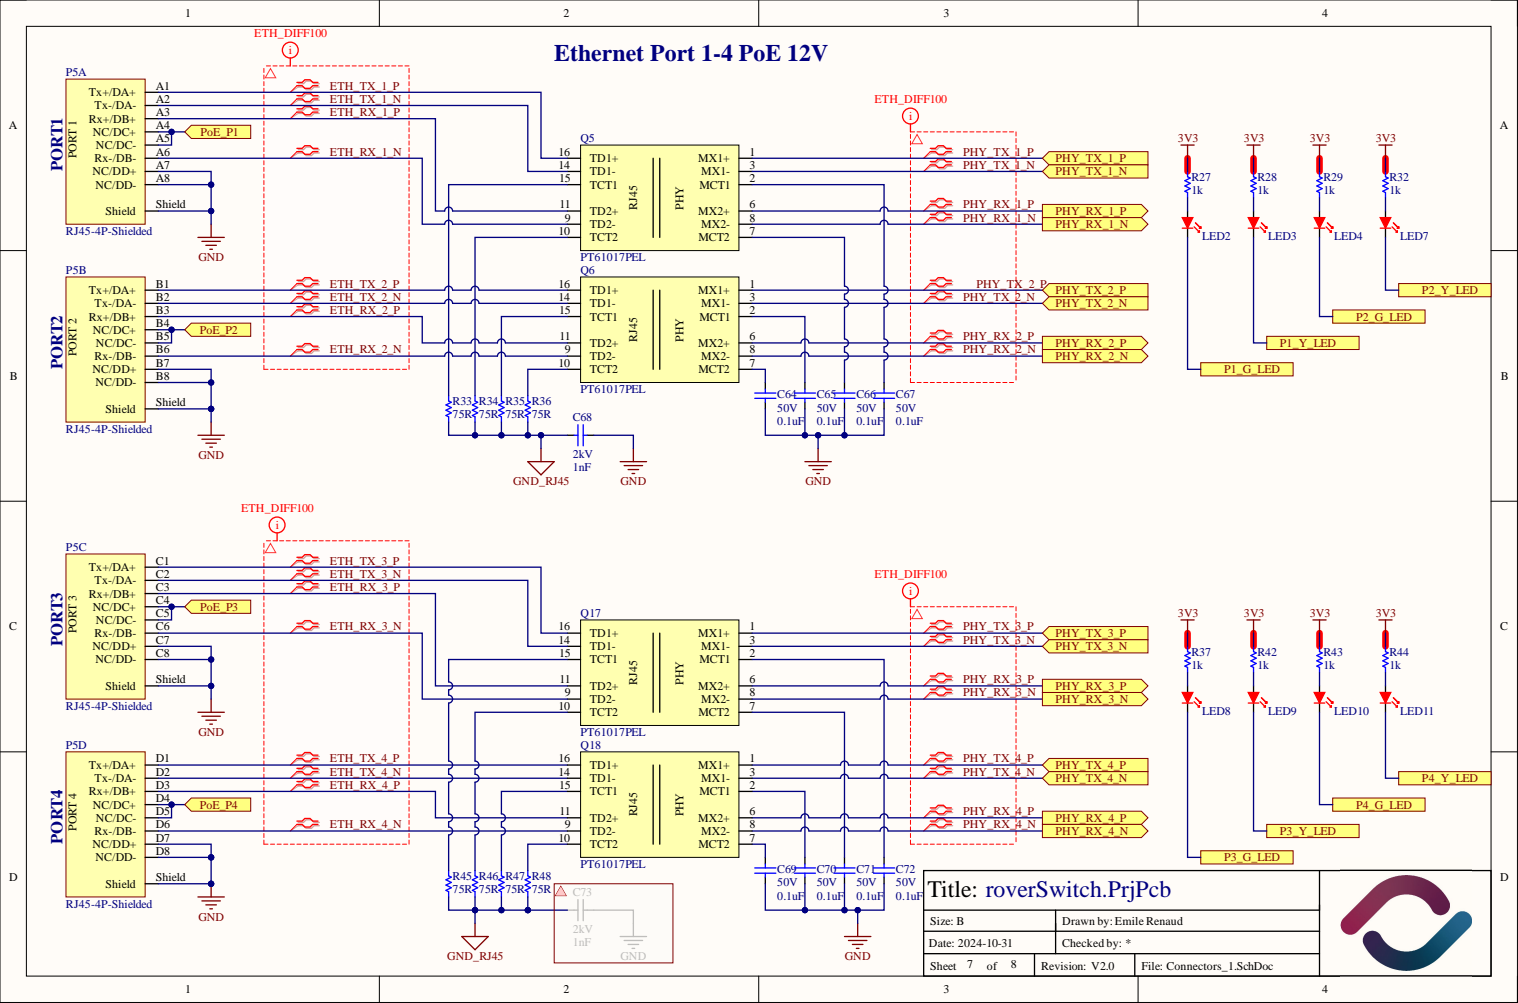
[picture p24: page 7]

A 2 | E T H _ T X_ 1 _N
A 3 | E T H _RX _ 1 _P
A 4 | | E T H _RX _ 1 _N

A 7 | 1 | 4
A 8 | | 1 5

Title: B roverSwitch.PrjPcb

Size : | Draw n b y : Emi le Renau d

Dat e : 4-1 - | Checked b y : *

Shee t o f | Rev i s i o n : V . 0 | Fi l e : Co n nect ors _ 1.S c h D o c

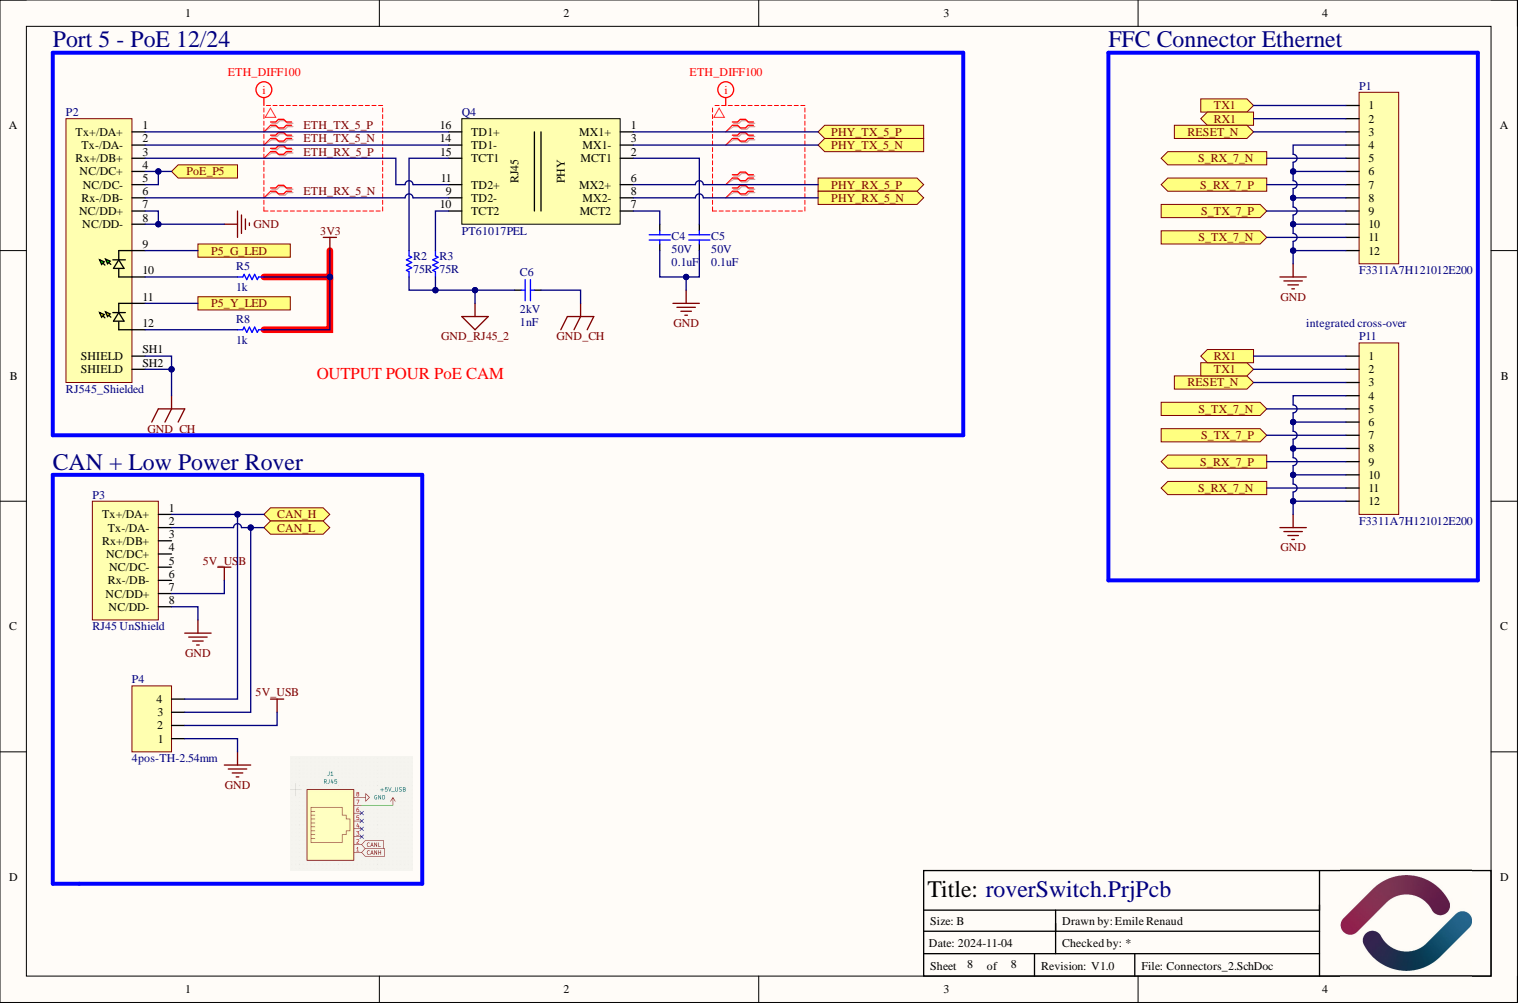
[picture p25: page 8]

OUTPUT POUR PoE CAM

CAN + Low Power Rover

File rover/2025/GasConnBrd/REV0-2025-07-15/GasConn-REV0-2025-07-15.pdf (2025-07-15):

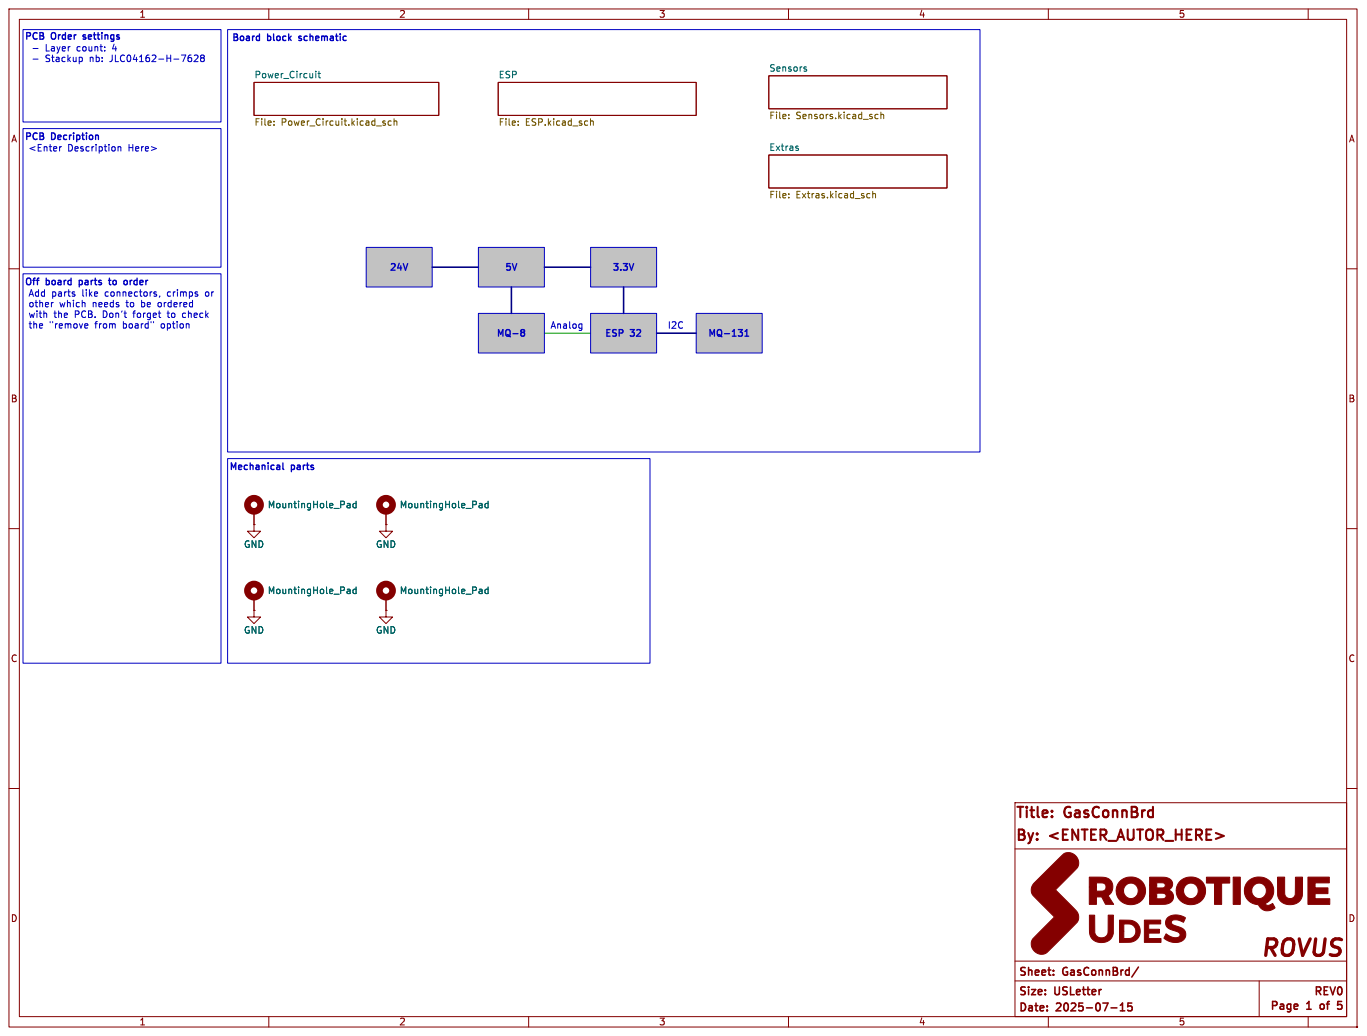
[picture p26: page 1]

3.3V Off board parts to order PCB Order settings
- Layer count: 4

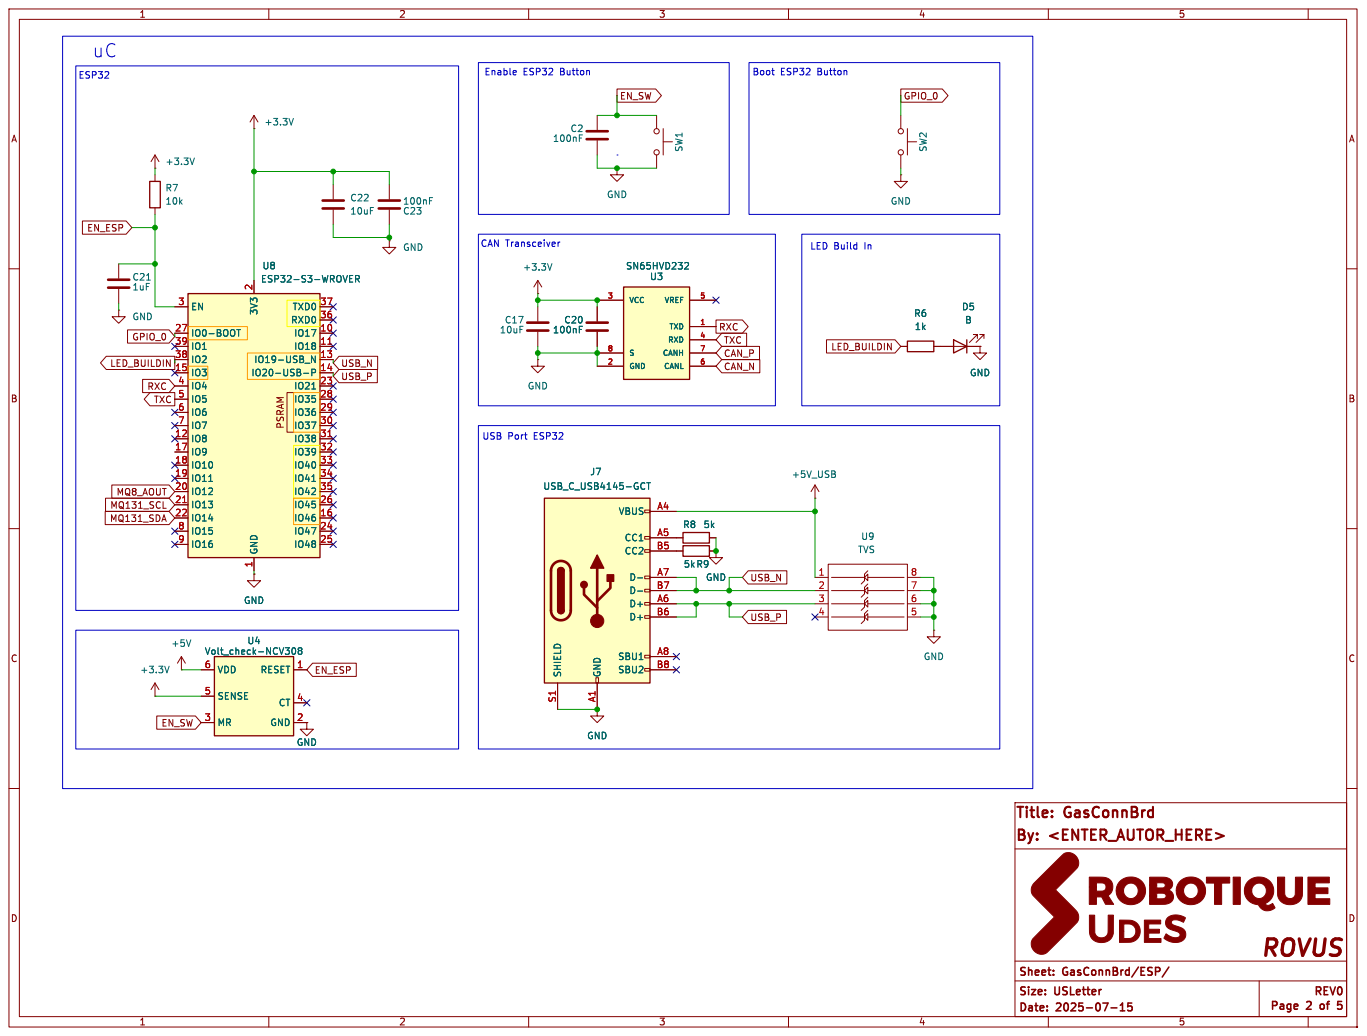
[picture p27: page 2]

LED Build In U8 ESP32-S3-WROVER

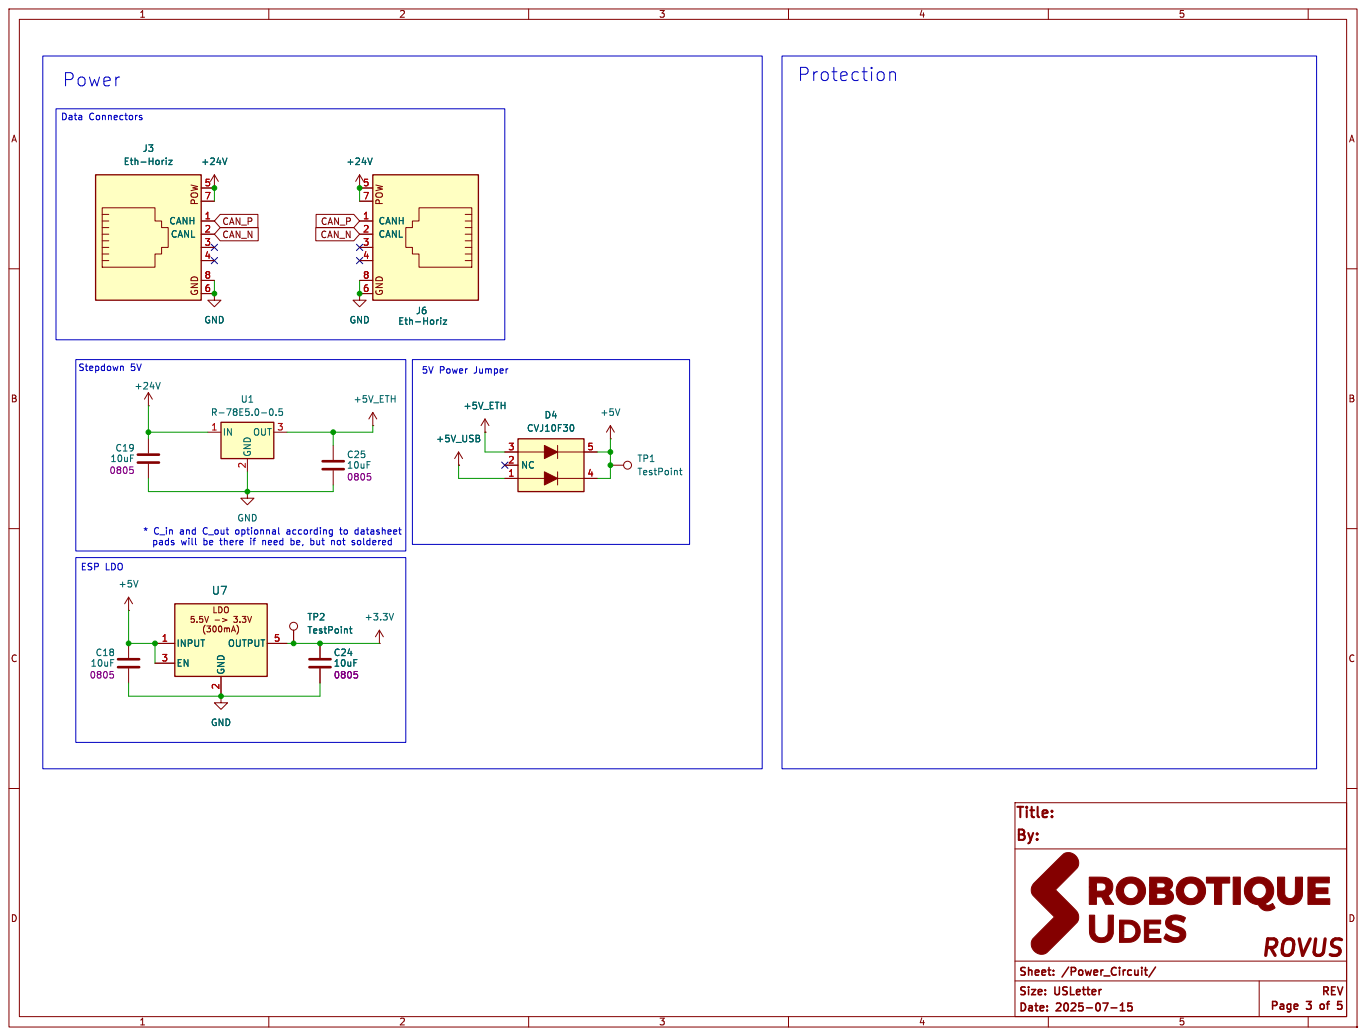
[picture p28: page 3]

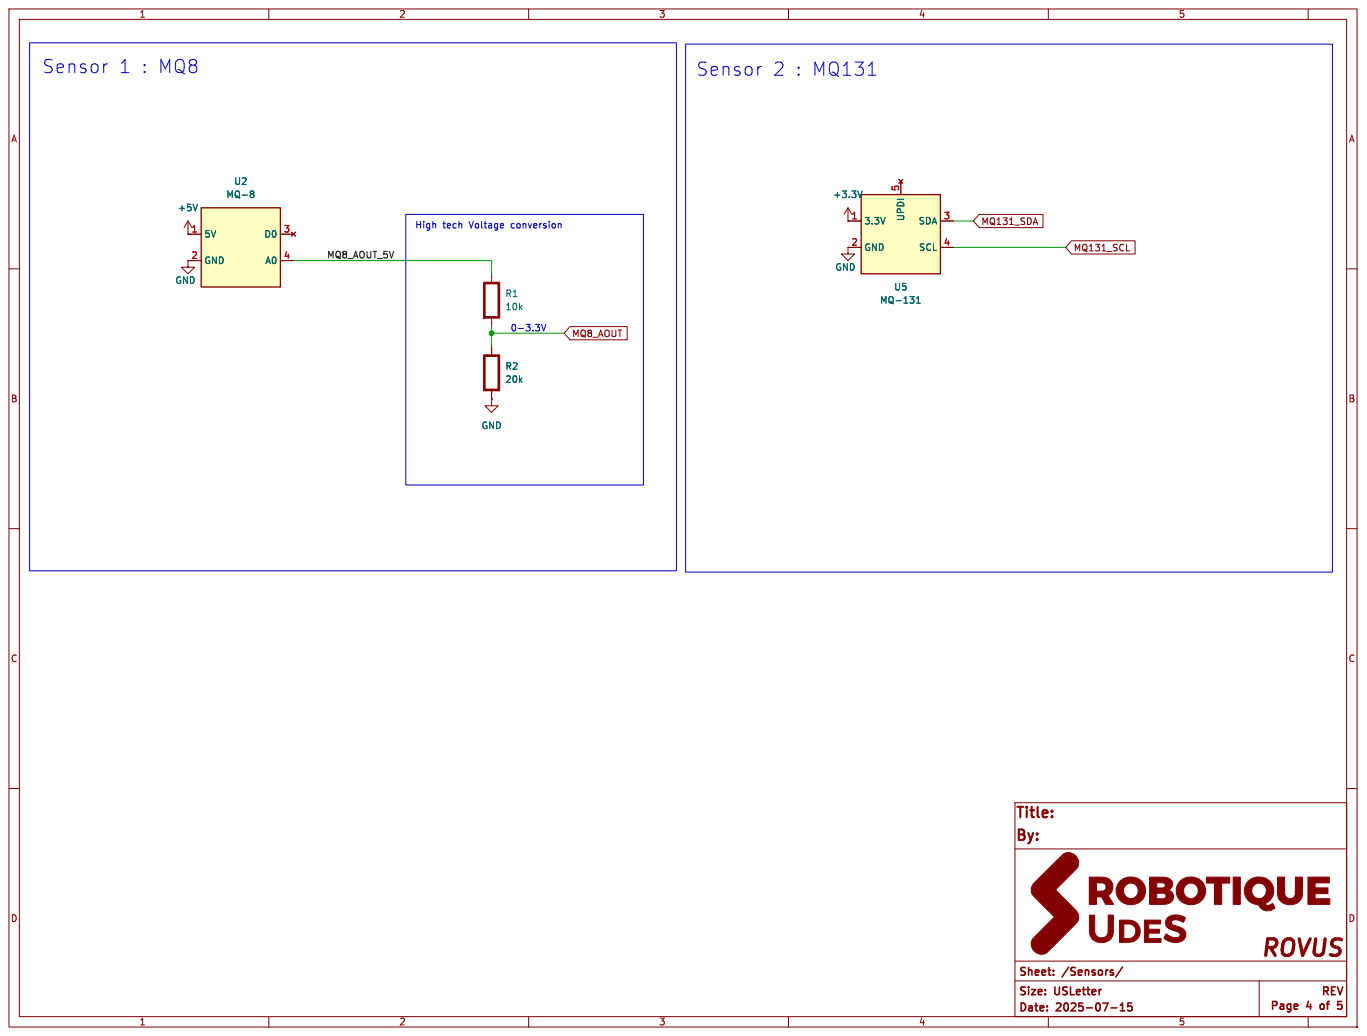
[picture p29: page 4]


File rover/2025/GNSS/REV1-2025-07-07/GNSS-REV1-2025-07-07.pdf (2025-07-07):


Data Connectors Power Jumper Enable ESP32 Button

Id: 1/1 Title: File: GNSS.kicad_sch Sheet: /

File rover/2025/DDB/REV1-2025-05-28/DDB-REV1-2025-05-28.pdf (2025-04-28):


TO BE VERIFIED GND

Boot ESP32 Button Data Input

J2 ETH-RJHSE508104 TO BE VERIFIED

J4 ETH-RJHSE508104 TO BE VERIFIED

4 J3 TerminalBlock TO BE VERIFIED

TO BE VERIFIED OUT 1 OUT 2 OUT 3

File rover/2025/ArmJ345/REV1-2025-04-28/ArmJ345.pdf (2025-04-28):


15A Trace PCB Decription PCB Order settings
- Layer count: 4
- Stackup nb: JLC04161-H-7628

(<6A) motor drivers to drive the

a current sensor on the driver's output. There's also a lidar in the gripper

to be stack over it to share 24V
and CAN




J5 ETH-RJHSE5081 TO BE VERIFIED



TO BE APPROVED GND

24_L(RJ45 conn) or 5V USB. Using a jumper to


J5 Motor Connector J5 Motor Driver

TO BE VERIFIED GND



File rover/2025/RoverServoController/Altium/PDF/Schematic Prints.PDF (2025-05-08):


Title: roverServoController.PrjPcb

Size: B | Drawn by: Emile Renaud

Date: 2024-12-05 | Checked by: *

Sheet 1 of 3 | Revision: V1.0 | File: Overview.SchDoc


Title: roverServoController.PrjPcb

Size: B | Drawn by: Emile Renaud

Date: 2024-12-07 | Checked by: *

Sheet 2 of 3 | Revision: V1.0 | File: ESP32.SchDoc


CDBA 5 4 0 -H F | 8 2 p F

Title: B roverServoController.PrjPcb

Size : | Draw n b y : Emi le Renau d

Dat e : 4-1 - | Checked b y : *

Shee t o f | Rev i s i o n : V . 0 | Fi l e : Po wer.Sch D o c































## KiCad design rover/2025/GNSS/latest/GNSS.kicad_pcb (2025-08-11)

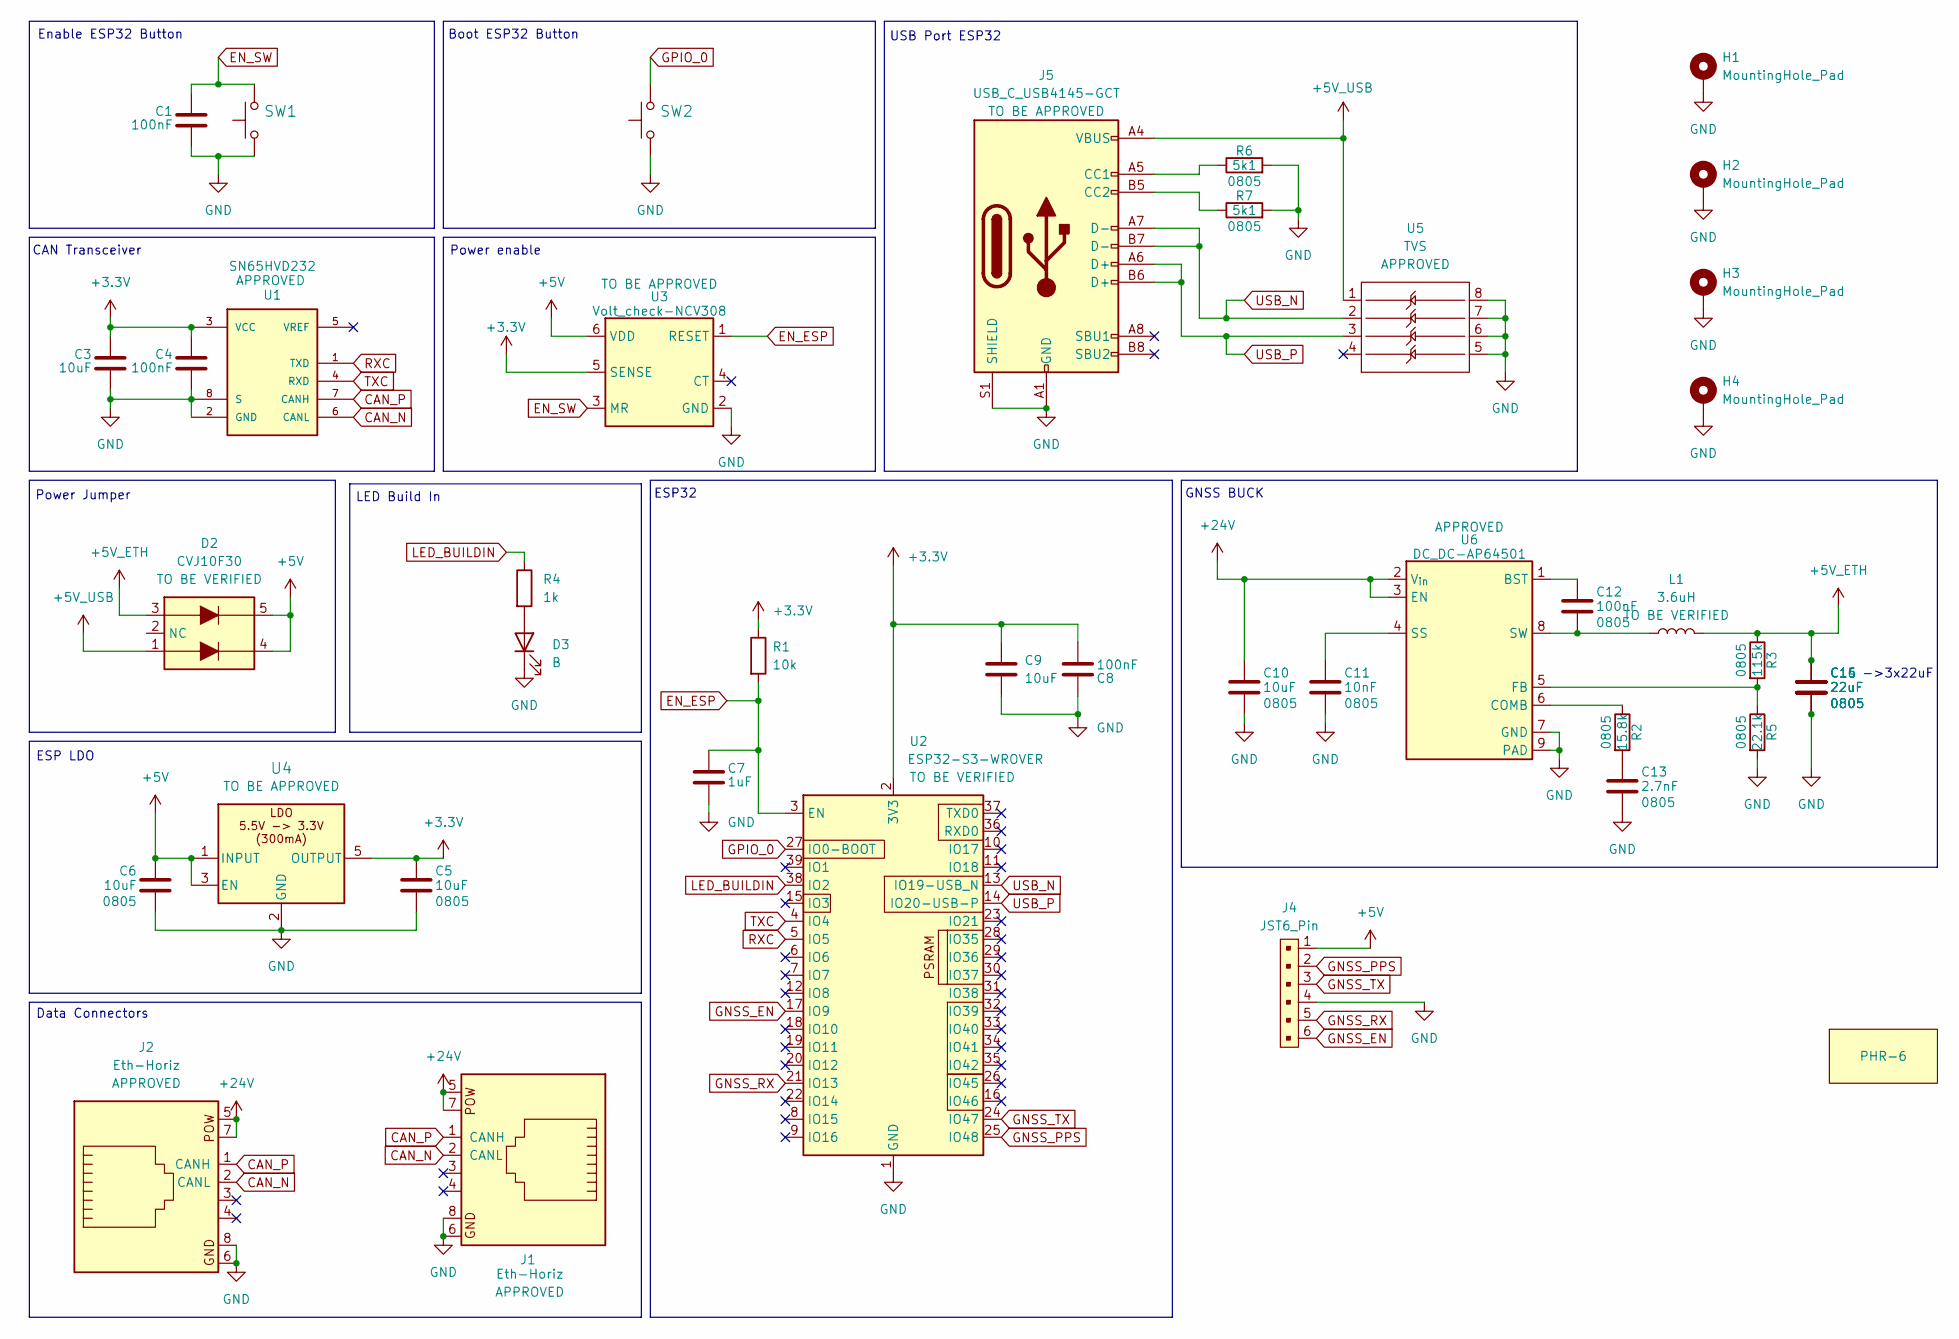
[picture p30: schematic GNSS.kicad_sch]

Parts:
C1, C4, C8, C12: 100nF; C_0805_2012Metric_Pad1.18x1.45mm_HandSolder
C3, C5, C6, C9, C10: 10uF; C_0805_2012Metric_Pad1.18x1.45mm_HandSolder
C7: 1uF; C_0805_2012Metric_Pad1.18x1.45mm_HandSolder
C11: 10nF; C_0805_2012Metric_Pad1.18x1.45mm_HandSolder
C13: 2.7nF; C_0805_2012Metric_Pad1.18x1.45mm_HandSolder
C14, C15, C16: 22uF; C_0805_2012Metric_Pad1.18x1.45mm_HandSolder
D2: CVJ10F30; Diode_schottky-CVJ10F30
D3: B; LED_0805_2012Metric_Pad1.15x1.40mm_HandSolder
G1: PHR-6
H1, H2, H3, H4: MountingHole_Pad; MountingHole_3.2mm_M3_DIN965_Pad_TopBottom
J1, J2: Eth-Horiz; Ethernet_Horizontal
J4: JST6_Pin; JST_PH_B6B-PH-K_1x06_P2.00mm_Vertical
J5: USB_C_USB4145-GCT; USB4145_GCT
L1: 3.6uH; L_3.6u_ASPI-6045S-3R6N-T
R1: 10k; R_0805_2012Metric_Pad1.20x1.40mm_HandSolder
R2: 15.8k; R_0805_2012Metric_Pad1.20x1.40mm_HandSolder
R3: 115k; R_0805_2012Metric_Pad1.20x1.40mm_HandSolder
R4: 1k; R_0805_2012Metric_Pad1.20x1.40mm_HandSolder
R5: 22.1k; R_0805_2012Metric_Pad1.20x1.40mm_HandSolder
R6, R7: 5k1; R_0805_2012Metric_Pad1.20x1.40mm_HandSolder
SW1, SW2: SW-PTS815SJM250SMTRLFS; SW-PTS815 SJM250SMTRLFS
U1: SN65HVD232; SOIC-8_3.9x4.9mm_P1.27mm; PARTREV 4
U2: ESP32-S3-WROVER; ESP32-S3-WROOM-1U
U3: Volt_check-NCV308; TSOP-6_1.65x3.05mm_P0.95mm
U4: LDO-TLV74033PDBVR; SOT-23-5_HandSoldering
U5: TVS; SOIC-8_3.9x4.9mm_P1.27mm
U6: DC_DC-AP64501; SOIC-8-1EP_3.9x4.9mm_P1.27mm_EP2.29x3mm

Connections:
+3.3V: C3.1, C4.1, C5.1, C8.2, C9.1, R1.1, U1.3 (VCC), U2.2 (3V3), U3.5 (SENSE), U4.5 (OUTPUT)
+5V: C6.1, D2.4, D2.5, J4.1, U3.6 (VDD), U4.1 (INPUT), U4.3 (EN)
+5V_ETH: C14.1, C15.1, C16.1, D2.3, L1.2, R3.1
+5V_USB: D2.1, J5.A4 (VBUS), J5.A9 (VBUS), J5.B4 (VBUS), J5.B9 (VBUS), U5.1
+24V: C10.1, J1.5, J1.7, J2.5, J2.7, U6.2 (V_{in}), U6.3 (EN)
CAN_N: J1.2 (CANL), J2.2 (CANL), U1.6 (CANL)
CAN_P: J1.1 (CANH), J2.1 (CANH), U1.7 (CANH)
EN_ESP: C7.1, R1.2, U2.3 (EN), U3.1 (RESET)
EN_SW: C1.1, SW1.4, U3.3 (MR)
GND: C1.2, C3.2, C4.2, C5.2, C6.2, C7.2, C8.1, C9.2, C10.2, C11.2, C13.2, C14.2, C15.2, C16.2, D3.1 (K), H1.1, H2.1, H3.1, H4.1, J1.6, J1.8, J2.6, J2.8, J4.4, J5.A1 (GND), J5.A12 (GND), J5.B1 (GND), J5.B12 (GND), J5.S1 (SHIELD), R5.2, R6.2, R7.2, SW1.1, SW1.2, SW2.1, SW2.2, U1.2 (GND), U1.8 (S), U2.1 (GND), U2.40 (GND), U2.41 (GND), U3.2 (GND), U4.2 (GND), U5.5, U5.6, U5.7, U5.8, U6.7 (GND), U6.9 (PAD)
GNSS_EN: J4.6, U2.17 (IO9)
GNSS_PPS: J4.2, U2.25 (IO48)
GNSS_RX: J4.5, U2.21 (IO13)
GNSS_TX: J4.3, U2.24 (IO47)
GPIO_0: SW2.4, U2.27 (IO0-BOOT)
LED_BUILDIN: R4.1, U2.38 (IO2)
unnamed: C13.1, R2.2
unnamed: D3.2 (A), R4.2
unnamed: J5.A5 (CC1), R6.1
unnamed: J5.B5 (CC2), R7.1
unnamed: C12.1, U6.1 (BST)
unnamed: R2.1, U6.6 (COMB)
unnamed: R3.2, R5.1, U6.5 (FB)
unnamed: C11.1, U6.4 (SS)
unnamed: C12.2, L1.1, U6.8 (SW)
RXC: U1.1 (TXD), U2.5 (IO5)
TXC: U1.4 (RXD), U2.4 (IO4)
USB_N: J5.A7 (D-), J5.B7 (D-), U2.13 (IO19-USB_N), U5.2
USB_P: J5.A6 (D+), J5.B6 (D+), U2.14 (IO20-USB-P), U5.3

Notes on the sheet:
Enable ESP32 Button
Power enable
->3x22uF
Data Connectors
Boot ESP32 Button
LED Build In
ESP32
CAN Transceiver
ESP LDO
GNSS BUCK
Power Jumper
USB Port ESP32

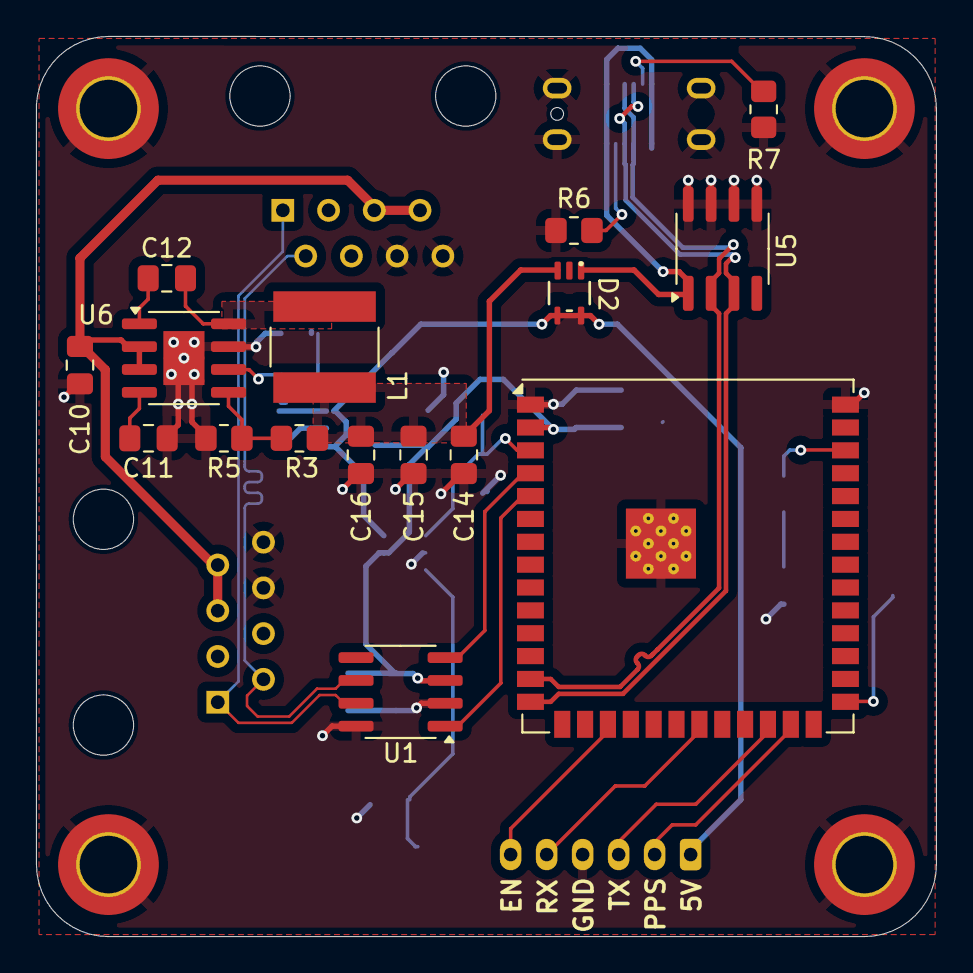
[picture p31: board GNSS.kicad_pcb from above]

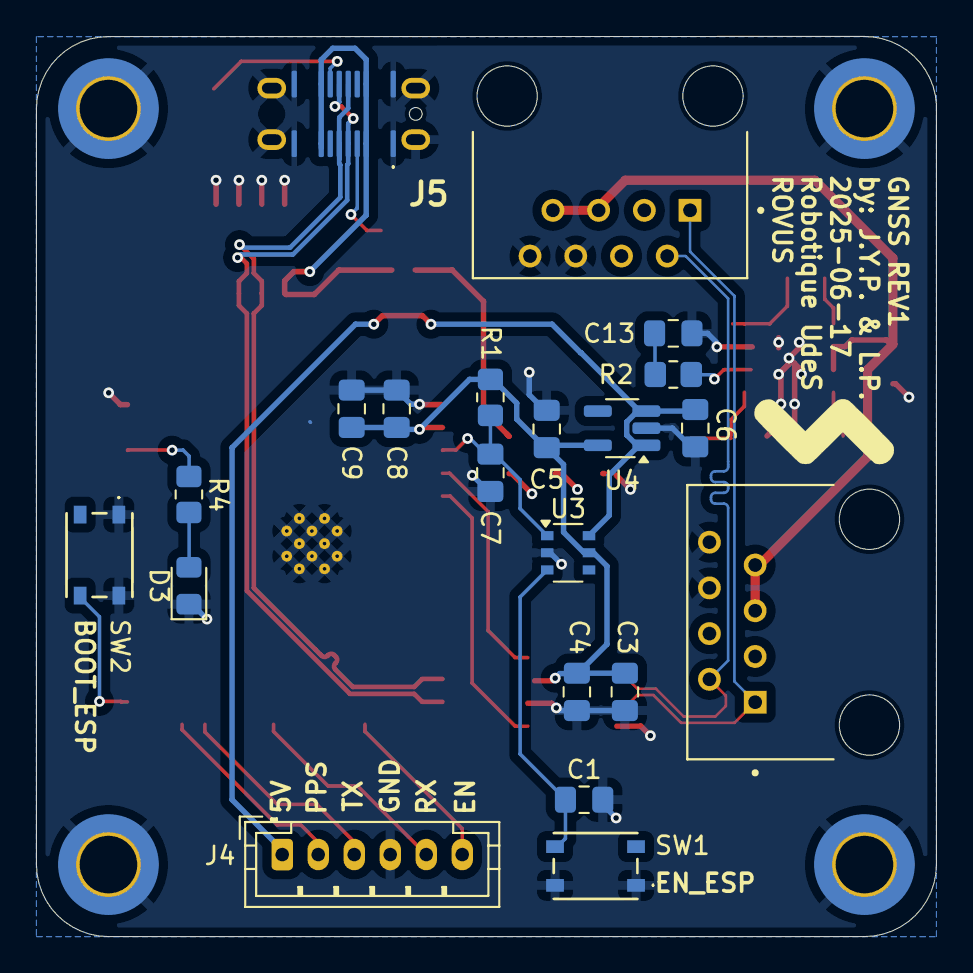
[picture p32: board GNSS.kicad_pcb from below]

Board: 4 copper layers, 50.0 x 50.0 mm, 41 parts (21 on the bottom side), 29 nets.

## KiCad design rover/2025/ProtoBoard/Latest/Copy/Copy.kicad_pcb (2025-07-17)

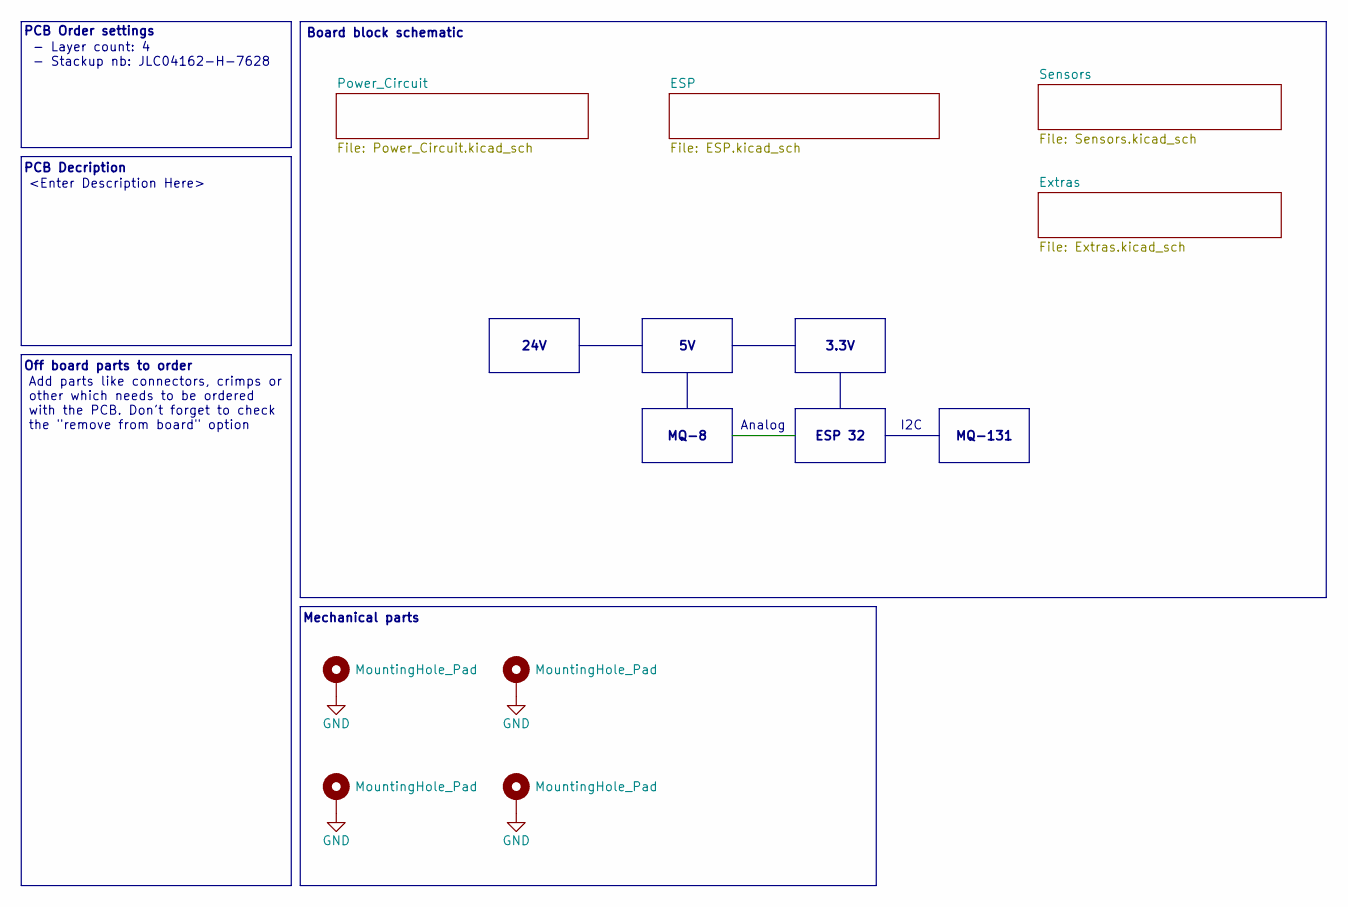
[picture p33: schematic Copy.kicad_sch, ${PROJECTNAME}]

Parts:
H9, H10, H11, H12: MountingHole_Pad; MountingHole

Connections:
GND: H9.1, H10.1, H11.1, H12.1; also elsewhere on the board

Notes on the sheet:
Off board parts to order
PCB Order settings
- Layer count: 4 - Stackup nb: JLC04162-H-7628
I2C
Analog
Board block schematic
Mechanical parts
PCB Decription
Add parts like connectors, crimps or other which needs to be ordered with the PCB. Don't forget to check the "remove from board" option
3.3V
24V
ESP 32
MQ-8
<Enter Description Here>
MQ-131

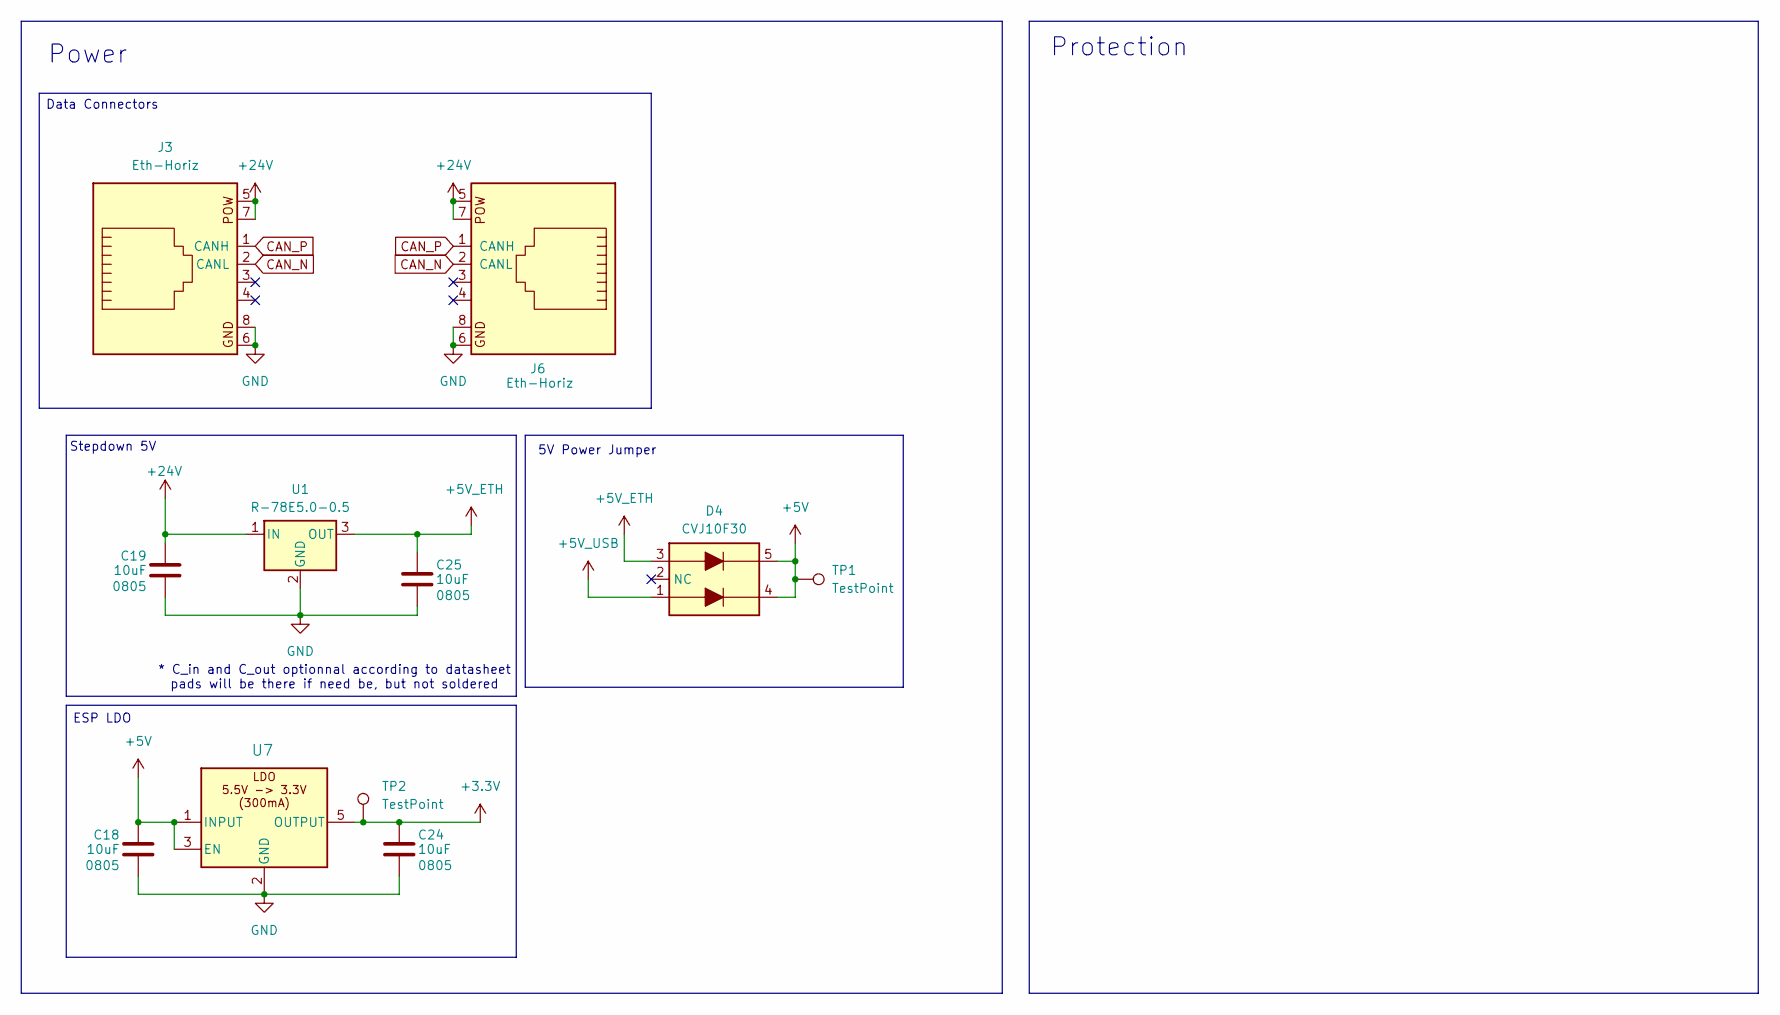
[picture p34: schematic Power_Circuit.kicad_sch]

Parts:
C18, C19, C24, C25: 10uF; C_0805_2012Metric_Pad1.18x1.45mm_HandSolder
D4: CVJ10F30; Diode_schottky-CVJ10F30
J3, J6: Eth-Horiz; Ethernet_Horizontal
TP1, TP2: TestPoint; TestPoint_Plated_Hole_D2.0mm
U1: R-78E5.0-0.5; Converter_DCDC_RECOM_R-78E-0.5_THT
U7: LDO-TLV74033PDBVR; SOT-23-5_HandSoldering

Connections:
+3.3V: C24.1, TP2.1, U7.5 (OUTPUT); also elsewhere on the board
+5V: C18.1, D4.4, D4.5, TP1.1, U7.1 (INPUT), U7.3 (EN); also elsewhere on the board
+5V_ETH: C25.1, D4.3, U1.3 (OUT)
+5V_USB: D4.1; also elsewhere on the board
+24V: C19.1, J3.5, J3.7, J6.5, J6.7, U1.1 (IN)
CAN_N: J3.2 (CANL), J6.2 (CANL); also elsewhere on the board
CAN_P: J3.1 (CANH), J6.1 (CANH); also elsewhere on the board
GND: C18.2, C19.2, C24.2, C25.2, J3.6, J3.8, J6.6, J6.8, U1.2 (GND), U7.2 (GND); also elsewhere on the board

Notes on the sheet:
ESP LDO
Power
Protection
5V Power Jumper
Stepdown 5V
* C_in and C_out optionnal according to datasheet pads will be there if need be, but not soldered
Data Connectors

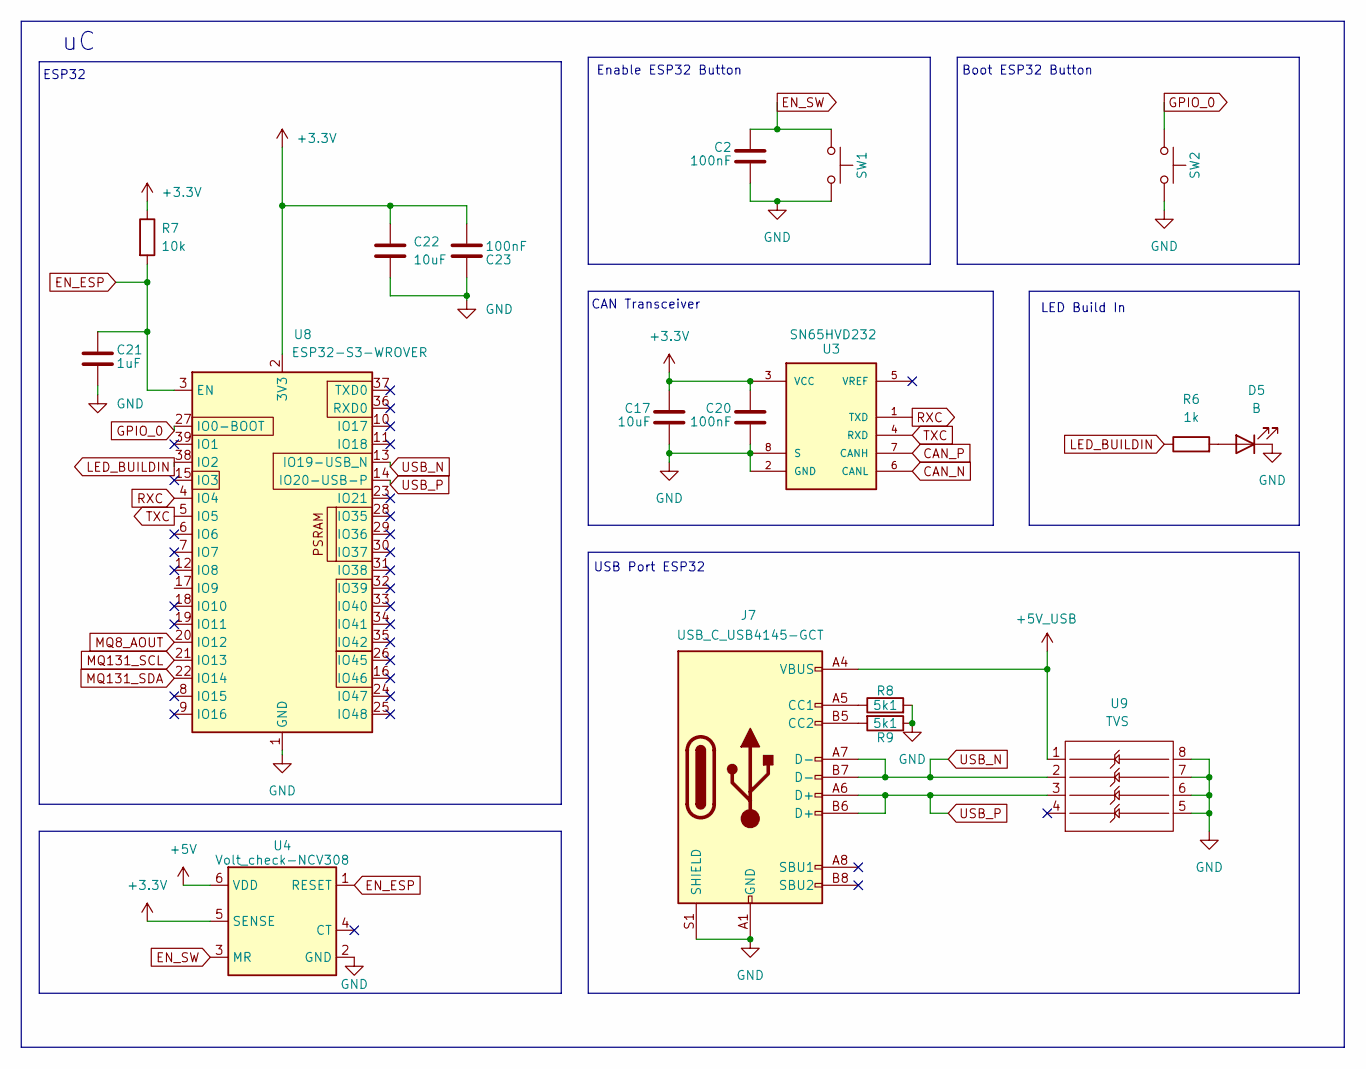
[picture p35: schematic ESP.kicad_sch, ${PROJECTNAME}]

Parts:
C2, C20, C23: 100nF; C_0805_2012Metric_Pad1.18x1.45mm_HandSolder
C17, C22: 10uF; C_0805_2012Metric_Pad1.18x1.45mm_HandSolder
C21: 1uF; C_0805_2012Metric_Pad1.18x1.45mm_HandSolder
D5: B; LED_0805_2012Metric_Pad1.15x1.40mm_HandSolder
J7: USB_C_USB4145-GCT; USB4145_GCT
R6: 1k; R_0805_2012Metric_Pad1.20x1.40mm_HandSolder
R7: 10k; R_0805_2012Metric_Pad1.20x1.40mm_HandSolder
R8, R9: 5k1; R_0805_2012Metric_Pad1.20x1.40mm_HandSolder
SW1, SW2: SW-PTS815SJM250SMTRLFS; SW-PTS815 SJM250SMTRLFS
U3: SN65HVD232; SOIC-8_3.9x4.9mm_P1.27mm; PARTREV 4
U4: Volt_check-NCV308; TSOP-6_1.65x3.05mm_P0.95mm; Digikey 488-NCV308SN500T1GCT-ND
U8: ESP32-S3-WROVER; ESP32-S3-WROOM-1U
U9: TVS; SOIC-8_3.9x4.9mm_P1.27mm

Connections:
+3.3V: C17.1, C20.1, C22.1, C23.2, R7.1, U3.3 (VCC), U4.5 (SENSE), U8.2 (3V3); also elsewhere on the board
+5V: U4.6 (VDD); also elsewhere on the board
+5V_USB: J7.A4 (VBUS), J7.A9 (VBUS), J7.B4 (VBUS), J7.B9 (VBUS), U9.1; also elsewhere on the board
CAN_N: U3.6 (CANL); also elsewhere on the board
CAN_P: U3.7 (CANH); also elsewhere on the board
EN_ESP: C21.1, R7.2, U4.1 (RESET), U8.3 (EN)
EN_SW: C2.1, SW1.1, SW1.2, U4.3 (MR)
GND: C2.2, C17.2, C20.2, C21.2, C22.2, C23.1, D5.1 (K), J7.A1 (GND), J7.A12 (GND), J7.B1 (GND), J7.B12 (GND), J7.S1 (SHIELD), R8.2, R9.1, SW1.4, SW2.4, U3.2 (GND), U3.8 (S), U4.2 (GND), U8.1 (GND), U8.40 (GND), U8.41 (GND), U9.5, U9.6, U9.7, U9.8; also elsewhere on the board
GPIO_0: SW2.1, SW2.2, U8.27 (IO0-BOOT)
LED_BUILDIN: R6.1, U8.38 (IO2)
MQ8_AOUT: U8.20 (IO12); also elsewhere on the board
MQ131_SCL: U8.21 (IO13); also elsewhere on the board
MQ131_SDA: U8.22 (IO14); also elsewhere on the board
unnamed: D5.2 (A), R6.2
unnamed: J7.A5 (CC1), R8.1
unnamed: J7.B5 (CC2), R9.2
RXC: U3.1 (TXD), U8.4 (IO4)
TXC: U3.4 (RXD), U8.5 (IO5)
USB_N: J7.A7 (D-), J7.B7 (D-), U8.13 (IO19-USB_N), U9.2
USB_P: J7.A6 (D+), J7.B6 (D+), U8.14 (IO20-USB-P), U9.3

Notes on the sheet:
LED Build In
Boot ESP32 Button
USB Port ESP32
Enable ESP32 Button
CAN Transceiver
ESP32

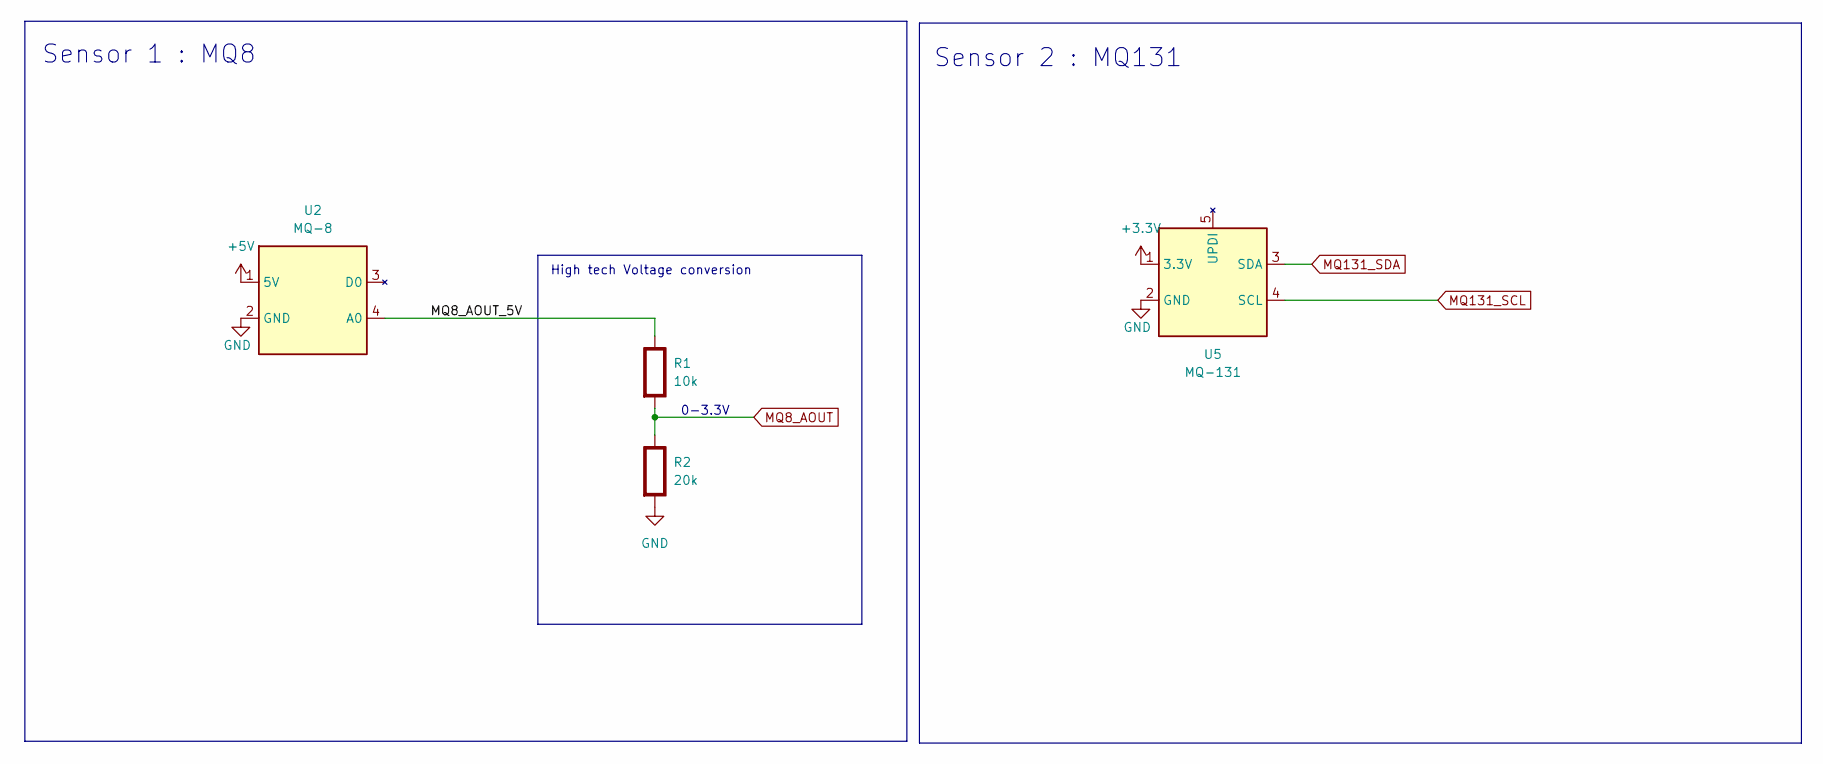
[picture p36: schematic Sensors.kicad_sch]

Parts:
R1: 10k; R_0805_2012Metric_Pad1.20x1.40mm_HandSolder; Rating W
R2: 20k; R_0805_2012Metric_Pad1.20x1.40mm_HandSolder; Rating W
U2: MQ-8; JST_PH_B4B-PH-SM4-TB_1x04-1MP_P2.00mm_Vertical
U5: MQ-131; JST_PH_B5B-PH-SM4-TB_1x05-1MP_P2.00mm_Vertical

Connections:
+3.3V: U5.1 (3.3V); also elsewhere on the board
+5V: U2.1 (5V); also elsewhere on the board
/Sensors/MQ8_AOUT_5V: R1.1 (+), U2.4 (A0)
GND: R2.2 (-), U2.2 (GND), U5.2 (GND); also elsewhere on the board
MQ8_AOUT: R1.2 (-), R2.1 (+); also elsewhere on the board
MQ131_SCL: U5.4 (SCL); also elsewhere on the board
MQ131_SDA: U5.3 (SDA); also elsewhere on the board

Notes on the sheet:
0-3.3V
High tech Voltage conversion
Sensor 1 : MQ8
Sensor 2 : MQ131

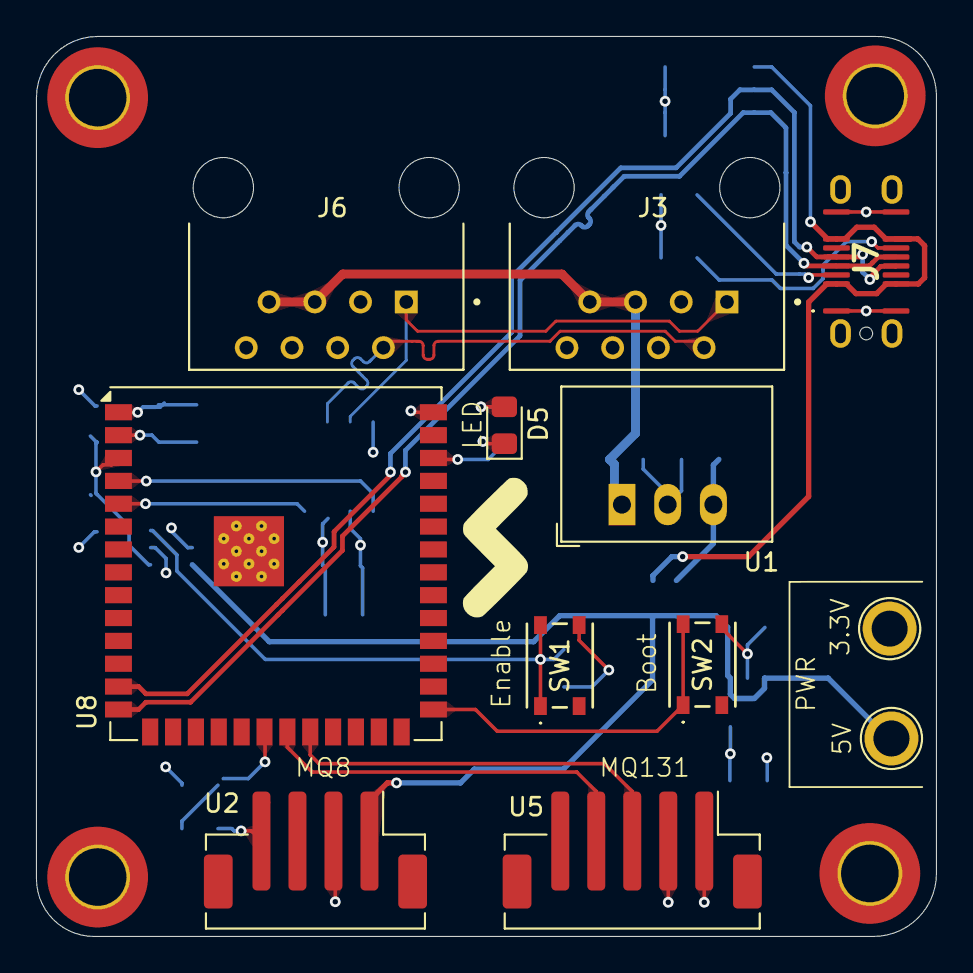
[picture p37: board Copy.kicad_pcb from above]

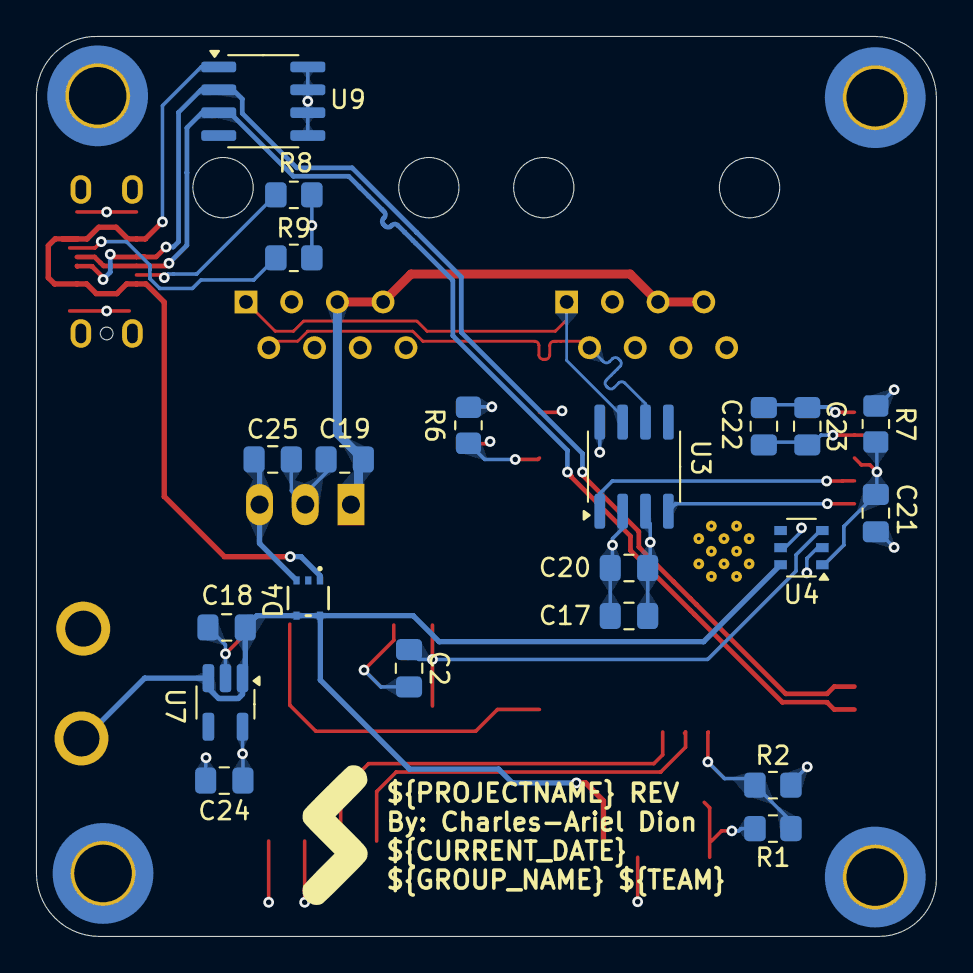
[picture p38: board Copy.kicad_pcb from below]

Board: 4 copper layers, 50.0 x 50.0 mm, 37 parts (21 on the bottom side), 23 nets.

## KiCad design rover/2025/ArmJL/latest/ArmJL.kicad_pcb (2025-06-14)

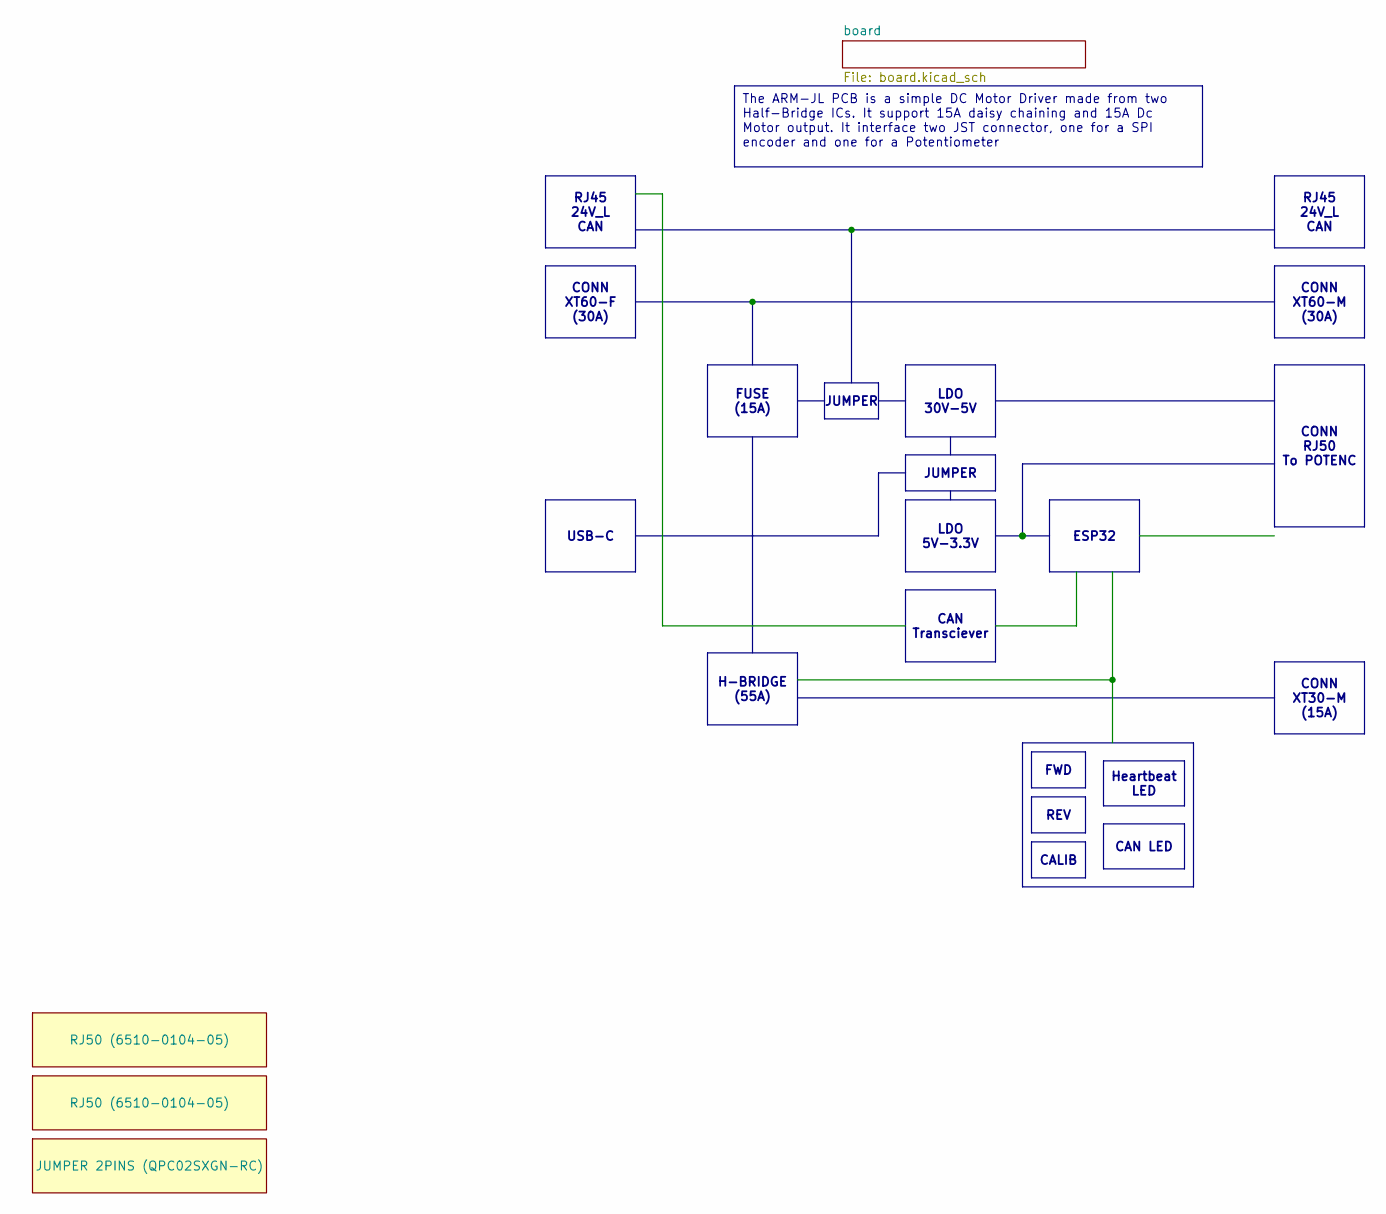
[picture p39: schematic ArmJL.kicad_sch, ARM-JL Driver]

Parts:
G1: JUMPER 2PINS (QPC02SXGN-RC)
G2, G3: RJ50 (6510-0104-05)

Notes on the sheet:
LDO 30V-5V
REV
CONN XT60-M (30A)
FWD
RJ45 24V_L CAN
FUSE (15A)
CAN LED
JUMPER
H-BRIDGE (55A)
Heartbeat LED
CONN XT60-F (30A)
CAN Transciever
USB-C
CONN RJ50 To POTENC
The ARM-JL PCB is a simple DC Motor Driver made from two Half-Bridge ICs. It support 15A daisy chaining and 15A Dc Motor output. It interface two JST connector, one for a SPI encoder and one for a Potentiometer
LDO 5V-3.3V
CALIB
ESP32
CONN XT30-M (15A)

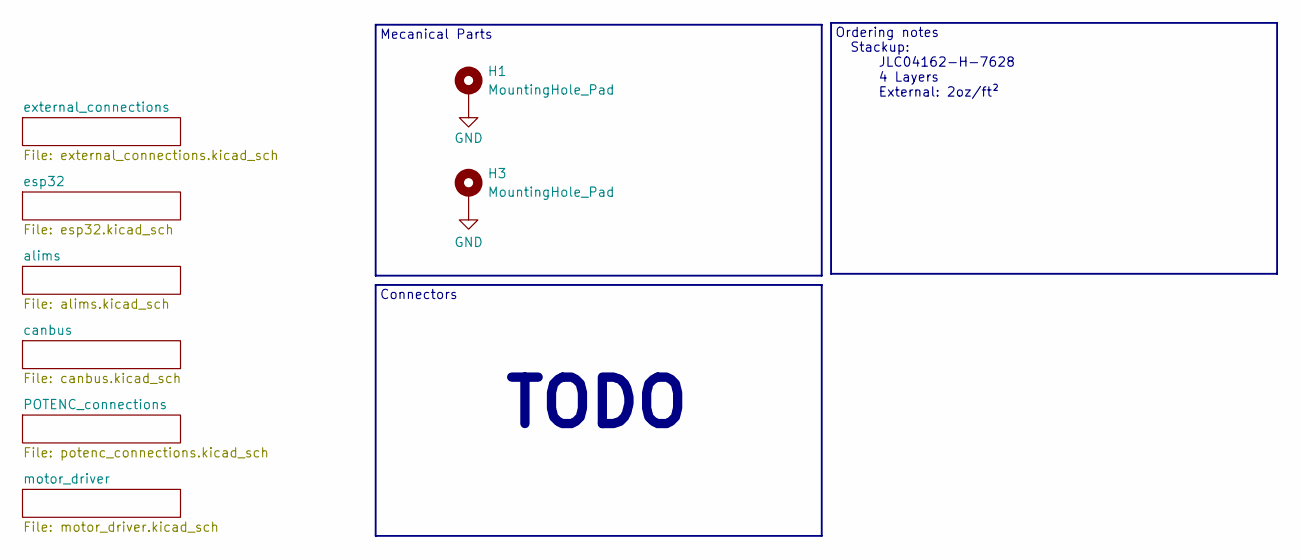
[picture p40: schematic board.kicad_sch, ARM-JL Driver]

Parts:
H1, H3: MountingHole_Pad; MountingHole_3.2mm_M3_DIN965_Pad_TopBottom

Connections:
GND: H1.1, H3.1; also elsewhere on the board

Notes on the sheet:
TODO
Mecanical Parts
Stackup: JLC04162-H-7628 4 Layers External: 2oz/ft²
Connectors
Ordering notes

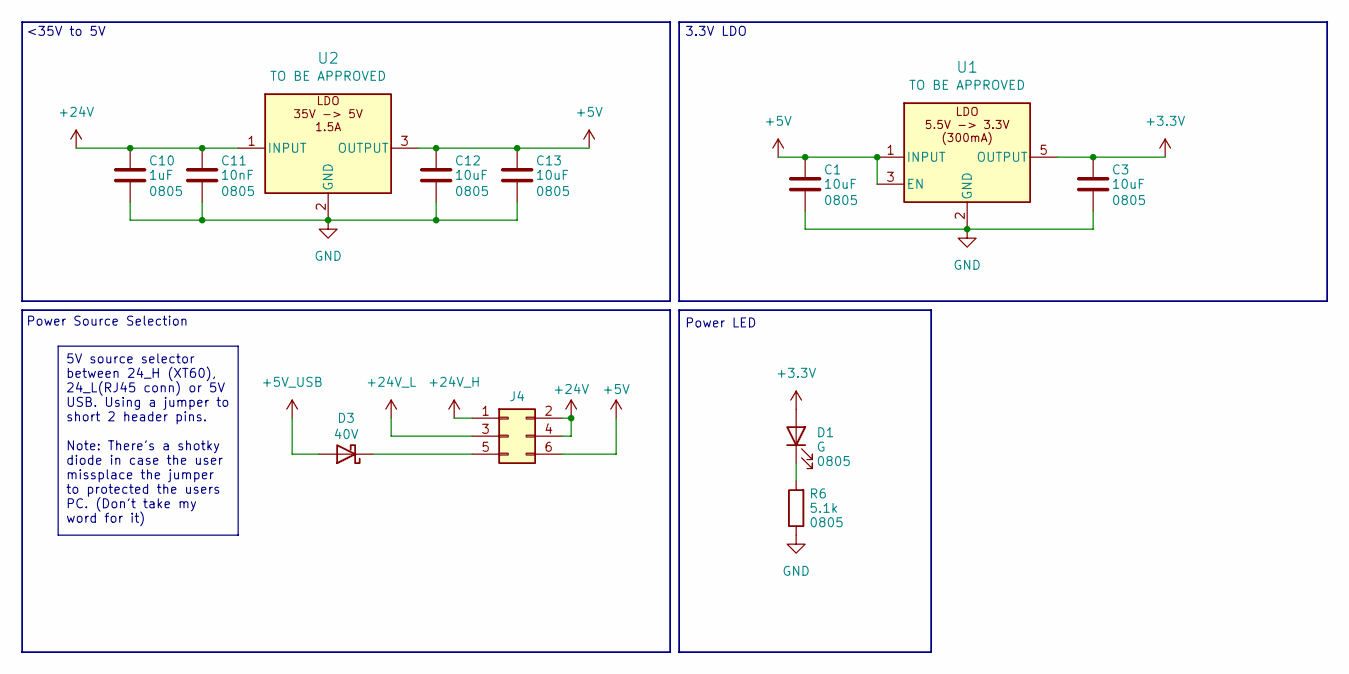
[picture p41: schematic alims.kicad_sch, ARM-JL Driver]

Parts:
C1, C3, C12, C13: 10uF; C_0805_2012Metric_Pad1.18x1.45mm_HandSolder
C10: 1uF; C_0805_2012Metric_Pad1.18x1.45mm_HandSolder
C11: 10nF; C_0805_2012Metric_Pad1.18x1.45mm_HandSolder
D1: G; LED_0805_2012Metric_Pad1.15x1.40mm_HandSolder
D3: 40V; D_SMA
J4: Conn_02x03_Odd_Even; PinHeader_2x03_P2.54mm_Vertical_SMD
R6: 5.1k; R_0805_2012Metric_Pad1.20x1.40mm_HandSolder
U1: LDO-TLV74033PDBVR; SOT-23-5_HandSoldering
U2: LDO-LM7805MPX/NOPB; SOT-223-3_TabPin2

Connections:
+3.3V: C3.1, D1.2 (A), U1.5 (OUTPUT); also elsewhere on the board
+5V: C1.1, C12.1, C13.1, J4.6, U1.1 (INPUT), U1.3 (EN), U2.3 (OUTPUT); also elsewhere on the board
+5V_USB: D3.2 (A); also elsewhere on the board
+24V: C10.1, C11.1, J4.2, J4.4, U2.1 (INPUT)
+24V_H: J4.1; also elsewhere on the board
+24V_L: J4.3; also elsewhere on the board
GND: C1.2, C3.2, C10.2, C11.2, C12.2, C13.2, R6.1, U1.2 (GND), U2.2 (GND); also elsewhere on the board
unnamed: D1.1 (K), R6.2
unnamed: D3.1 (K), J4.5

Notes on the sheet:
5V source selector between 24_H (XT60), 24_L(RJ45 conn) or 5V USB. Using a jumper to short 2 header pins. Note: There's a shotky diode in case the user missplace the jumper to protected the users PC. (Don't take my word for it)
3.3V LDO
Power LED
<35V to 5V
Power Source Selection

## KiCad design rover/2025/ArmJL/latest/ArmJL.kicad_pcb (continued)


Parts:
F2: 15A; FuseHolder-3588-20
J1: USB_C_USB4105-GF-A; USB4145_GCT
J2, J6: ETH-RJHSE5081
R1, R2, R3, R4: 5.1k; R_0805_2012Metric_Pad1.20x1.40mm_HandSolder
U5: XT60PW-M; AMASS_XT60PW-M_1x02_P7.20mm_Horizontal
U6: XT60PM-F; AMASS_XT60PW-F_1x02_P7.20mm_Horizontal

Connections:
+5V_USB: J1.A4 (VBUS), J1.A9 (VBUS), J1.B4 (VBUS), J1.B9 (VBUS); also elsewhere on the board
+24V_H: F2.1; also elsewhere on the board
+24V_L: J2.5 (Vcc), J2.7 (Vcc), J2.10 (G_L+), J6.5 (Vcc), J6.7 (Vcc), J6.10 (G_L+); also elsewhere on the board
CAN_N: J2.2 (CANL), J6.2 (CANL); also elsewhere on the board
CAN_P: J2.1 (CANH), J6.1 (CANH); also elsewhere on the board
GND: J1.A1 (GND), J1.A12 (GND), J1.B1 (GND), J1.B12 (GND), J2.6 (GND), J2.8 (GND), J6.6 (GND), J6.8 (GND), R1.2, R2.2, R3.2, R4.2, U5.1 (-), U6.1 (-); also elsewhere on the board
unnamed: J1.A5 (CC1), R1.1
unnamed: J1.B5 (CC2), R2.1
unnamed: J2.9 (G_L-), R3.1
unnamed: J6.9 (G_L-), R4.1
unnamed: F2.2, U5.2 (+), U6.2 (+)
USB_N: J1.A7 (D-), J1.B7 (D-); also elsewhere on the board
USB_P: J1.A6 (D+), J1.B6 (D+); also elsewhere on the board

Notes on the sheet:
Data daisy chain
USB-C
Power daisy chain


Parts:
C14: 470uF; CP_Elec_10x12.6
C17, C22: 100nF; C_0805_2012Metric_Pad1.18x1.45mm_HandSolder
C18, C19, C20, C21: 220nF; C_0805_2012Metric_Pad1.18x1.45mm_HandSolder
J5: XT30PW-F; AMASS_XT30PW-F_1x02_P2.50mm_Horizontal; PARTREV 1.2
R8, R9: 10k; R_0805_2012Metric_Pad1.20x1.40mm_HandSolder
SW3, SW4: SW-PTS815SJM250SMTRLFS; SW-PTS815 SJM250SMTRLFS
U7, U8: IFX007TAUMA1; TO-263-7_TabPin4

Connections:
+3.3V: R8.2, R9.2; also elsewhere on the board
+24V_H: C14.1, C17.1, C18.1, C20.1, C22.1, U7.7 (VS), U8.7 (VS); also elsewhere on the board
/board/motor_driver/M_OUT_A: C19.1, C20.2, J5.2 (+), U7.4 (OUT)
/board/motor_driver/M_OUT_B: C18.2, C21.1, J5.1 (-), U8.4 (OUT)
GND: C14.2, C17.2, C19.2, C21.2, C22.2, SW3.1, SW3.2, SW4.1, SW4.2, U7.1 (GND), U7.5 (SR), U8.1 (GND), U8.5 (SR); also elsewhere on the board
M_EN_A: U7.3 (EN_(INH)); also elsewhere on the board
M_EN_B: U8.3 (EN_(INH)); also elsewhere on the board
M_IN_A: U7.2 (IN); also elsewhere on the board
M_IN_B: U8.2 (IN); also elsewhere on the board
PB_FWD: R8.1, SW3.4; also elsewhere on the board
PB_REV: R9.1, SW4.4; also elsewhere on the board

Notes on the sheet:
With the SR at 0V, the T_{r} is ~0.25us. Per datasheet, the maximum switching frequency should be: 1us / (10 x T_{r}) = 400kHz Note: Switching fondamental frequency is about 1.5-2Mhz for decoupling
Motor Manual Controls
H-Bridge
Motor Output Connector


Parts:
J3: RJ50-SS-641010-A-NF-A111
R10: 10k; R_0805_2012Metric_Pad1.20x1.40mm_HandSolder
SW5: SW-PTS815SJM250SMTRLFS; SW-PTS815 SJM250SMTRLFS

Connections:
+3.3V: J3.1, R10.2; also elsewhere on the board
+5V: J3.2; also elsewhere on the board
ENC_CS: J3.7; also elsewhere on the board
ENC_MISO: J3.6; also elsewhere on the board
ENC_MOSI: J3.4; also elsewhere on the board
ENC_SCLK: J3.3; also elsewhere on the board
GND: J3.5, J3.10, SW5.1, SW5.2; also elsewhere on the board
PB_CALIB: R10.1, SW5.4; also elsewhere on the board
POT_ANAL: J3.9; also elsewhere on the board

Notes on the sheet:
The POTENC is a breakout board with a connection to a SameSky AMT22-X encoder and a connection to a 10 turn potentiometer. The combinaison of both creates a 10 turns absolute encoder
Connections to POTENC connector
POTENC Calibration button


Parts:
C5: 22uF; C_0805_2012Metric_Pad1.18x1.45mm_HandSolder
C6, C8, C9: 100nF; C_0805_2012Metric_Pad1.18x1.45mm_HandSolder
C7: 1uF; C_0805_2012Metric_Pad1.18x1.45mm_HandSolder
R5: 10k; R_0805_2012Metric_Pad1.20x1.40mm_HandSolder
SW1, SW2: SW-PTS815SJM250SMTRLFS; SW-PTS815 SJM250SMTRLFS
U4: ESP32-S3-WROVER; ESP32-S3-WROOM-1U

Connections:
+3.3V: C5.1, C6.1, R5.1, U4.2 (3V3); also elsewhere on the board
/board/esp32/BOOT_PB: C9.2, SW2.1, SW2.2, U4.27 (IO0-BOOT)
/board/esp32/EN_PB: C7.1, C8.2, R5.2, SW1.1, SW1.2, U4.3 (EN)
CAN_RX: U4.17 (IO9); also elsewhere on the board
CAN_TX: U4.18 (IO10); also elsewhere on the board
ENC_CS: U4.7 (IO7); also elsewhere on the board
ENC_MISO: U4.4 (IO4); also elsewhere on the board
ENC_MOSI: U4.5 (IO5); also elsewhere on the board
ENC_SCLK: U4.6 (IO6); also elsewhere on the board
GND: C5.2, C6.2, C7.2, C8.1, C9.1, SW1.4, SW2.4, U4.1 (GND), U4.40 (GND), U4.41 (GND); also elsewhere on the board
LED_CAN: U4.23 (IO21); also elsewhere on the board
M_EN_A: U4.38 (IO2); also elsewhere on the board
M_EN_B: U4.24 (IO47); also elsewhere on the board
M_IN_A: U4.39 (IO1); also elsewhere on the board
M_IN_B: U4.25 (IO48); also elsewhere on the board
PB_CALIB: U4.21 (IO13); also elsewhere on the board
PB_FWD: U4.22 (IO14); also elsewhere on the board
PB_REV: U4.31 (IO38); also elsewhere on the board
POT_ANAL: U4.8 (IO15); also elsewhere on the board
USB_N: U4.13 (IO19-USB_N); also elsewhere on the board
USB_P: U4.14 (IO20-USB-P); also elsewhere on the board

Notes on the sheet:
ESP32 Buttons


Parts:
C15: 100nF; C_0805_2012Metric_Pad1.18x1.45mm_HandSolder
C16: 10uF; C_0805_2012Metric_Pad1.18x1.45mm_HandSolder
D2: B; LED_0805_2012Metric_Pad1.15x1.40mm_HandSolder
R7: 5.1k; R_0805_2012Metric_Pad1.20x1.40mm_HandSolder
U3: SN65HVD232; SOIC-8_3.9x4.9mm_P1.27mm; PARTREV 4

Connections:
+3.3V: C15.1, C16.1, U3.3 (VCC); also elsewhere on the board
CAN_N: U3.6 (CANL); also elsewhere on the board
CAN_P: U3.7 (CANH); also elsewhere on the board
CAN_RX: U3.1 (TXD); also elsewhere on the board
CAN_TX: U3.4 (RXD); also elsewhere on the board
GND: C15.2, C16.2, R7.1, U3.2 (GND), U3.8 (S); also elsewhere on the board
LED_CAN: D2.2 (A); also elsewhere on the board
unnamed: D2.1 (K), R7.2

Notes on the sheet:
CAN Transciever
CAN LED



Board: 4 copper layers, 79.5 x 36.0 mm, 55 parts (36 on the bottom side), 38 nets.

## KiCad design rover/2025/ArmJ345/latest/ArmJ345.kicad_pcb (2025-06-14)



Board: 4 copper layers, 100.0 x 80.0 mm, 97 parts (40 on the bottom side), 63 nets.

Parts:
C1: 470uF; CP_Elec_8x10.5
C2, C4, C6, C14, C16, C17, C18, C19, C21, C23, C25: 100nF; C_0805_2012Metric_Pad1.18x1.45mm_HandSolder
C3, C5, C9, C10, C11, C12, C13, C20, C22, C24: 10uF; C_0805_2012Metric_Pad1.18x1.45mm_HandSolder
C7: 1nF; C_0805_2012Metric_Pad1.18x1.45mm_HandSolder
C8: 4.7nF; C_0805_2012Metric_Pad1.18x1.45mm_HandSolder
C15: 1uF; C_0805_2012Metric_Pad1.18x1.45mm_HandSolder
D1: G; LED_0805_2012Metric_Pad1.15x1.40mm_HandSolder
D2: 40V; D_SMA
D3, D4: B; LED_0805_2012Metric_Pad1.15x1.40mm_HandSolder
F1: 15A; FuseHolder-3588-20
H1, H2, H3, H4: MountingHole_Pad; MountingHole_3.2mm_M3_DIN965_Pad_TopBottom
J1: JST_PH_SB6; JST_PH_S6B-PH-SM4-TB_1x06-1MP_P2.00mm_Horizontal
J2: XT30PW-M; AMASS_XT30PW-M_1x02_P2.50mm_Horizontal
J3: USB_C_USB4105-GF-A; USB_C_Receptacle_GCT_USB4105-xx-A_16P_TopMnt_Horizontal
J4: Conn_01x04_Socket; PinSocket_1x04_P2.54mm_Vertical_SMD_Pin1Left
J5: ETH-RJHSE5081
J6: Conn_02x03_Odd_Even; PinHeader_2x03_P2.54mm_Vertical_SMD
J7, J8: XT30PW-M; AMASS_XT30PW-F_1x02_P2.50mm_Horizontal
J9, J10: JST-PH-S6B; JST_PH_S6B-PH-SM4-TB_1x06-1MP_P2.00mm_Horizontal
J11: Conn_01x04_MountingPin; JST_PH_S4B-PH-SM4-TB_1x04-1MP_P2.00mm_Horizontal
J13: Conn_01x02_MountingPin; JST_PH_S2B-PH-SM4-TB_1x02-1MP_P2.00mm_Horizontal
J14: Conn_01x03_MountingPin; JST_PH_S3B-PH-SM4-TB_1x03-1MP_P2.00mm_Horizontal
R1, R2, R3, R11, R14, R15, R16, R17, R18, R19, R21, R22, R23, R24, R25, R26, R27, R28, R31, R32, R33: 10k; R_0805_2012Metric_Pad1.20x1.40mm_HandSolder
R4: 0.05 (CRA2512-FZ-R050ELF); R_2512_6332Metric_Pad1.40x3.35mm_HandSolder
R5, R6, R7, R10, R29, R30: 5.1k; R_0805_2012Metric_Pad1.20x1.40mm_HandSolder
R8, R9: 60.4; R_0805_2012Metric_Pad1.20x1.40mm_HandSolder
R12, R13: 4.7k; R_0805_2012Metric_Pad1.20x1.40mm_HandSolder
SW1, SW2, SW3, SW4, SW5, SW6, SW7, SW8, SW9: SW-PTS815SJM250SMTRLFS; SW-PTS815 SJM250SMTRLFS
U1, U8, U9: IFX9201SGAUMA1; DRIVE_IFX9201SGAUMA1
U2: CURR_SENSE-INA219AIDCNTG4; SOT-23-8
U3: TVS-SMDB03CE3; SOIC-8_3.9x4.9mm_P1.27mm
U4: SN65HVD232; SOIC-8_3.9x4.9mm_P1.27mm
U5: LDO-LM340SX-5.0/NOPB; TO-263-3_TabPin2
U6: LDO-TLV74033PDBVR; SOT-23-5_HandSoldering
U7: ESP32-S3-WROVER; ESP32-S3-WROOM-1U

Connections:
+3.3V: C3.1, C4.1, C5.1, C6.1, C12.1, C13.1, C14.1, C20.1, C21.1, C22.1, C23.1, C24.1, C25.1, D1.2 (A), J1.2, J11.1, R11.1, R12.1, R13.1, R21.1, R22.1, R23.1, R24.1, R25.1, R26.1, R27.1, R28.1, R31.1, R32.1, R33.1, U1.2 (VSO), U2.4 (VS), U2.7 (A0), U2.8 (A1), U4.3 (VCC), U4.5 (VREF), U6.5 (OUTPUT), U7.2 (3V3), U8.2 (VSO), U9.2 (VSO)
+5V: C10.1, C11.1, J6.6, J9.1, J10.1, J14.2, U5.3 (OUTPUT), U6.1 (INPUT), U6.3 (EN)
+5V_USB: D2.2 (A), J3.A4 (VBUS), J3.A9 (VBUS), J3.B4 (VBUS), J3.B9 (VBUS), U3.1
+24V: C9.1, J6.2, J6.4, U5.1 (INPUT)
+24V_H: C1.1, C2.1, C18.1, C19.1, F1.1, J6.1, U1.4 (VS), U8.4 (VS), U9.4 (VS)
+24V_L: J4.2, J5.5 (Vcc), J5.7 (Vcc), J5.10 (G_L+), J6.3
/Board/drive_j5/M5_A: J1.6, U1.7 (OUT2)
/Board/drive_j5/M5_B: J1.1, R4.2, U2.2 (IN-)
/Board/drive_j5/SENSE_+: R4.1, U1.5 (OUT1), U2.1 (IN+)
/Board/esp32/BOOT_PB: C17.2, SW2.1, SW2.2, U7.27 (IO0-BOOT)
/Board/esp32/CAN_LED: D3.2 (A), U7.17 (IO9)
/Board/esp32/EN_PB: C15.1, C16.2, R11.2, SW1.1, SW1.2, U7.3 (EN)
/Board/esp32/USER_LED: D4.2 (A), U7.6 (IO6)
/Board/external_connections/CC1: J3.A5 (CC1), R5.1
/Board/external_connections/CC2: J3.B5 (CC2), R6.1
CAN_N: J4.3, J5.2 (CANL), R9.1, U4.6 (CANL)
CAN_P: J4.4, J5.1 (CANH), R8.2, U4.7 (CANH)
CAN_RX: U4.4 (RXD), U7.5 (IO5)
CAN_TX: U4.1 (TXD), U7.4 (IO4)
GND: C1.2, C2.2, C3.2, C4.2, C5.2, C6.2, C7.2, C8.2, C9.2, C10.2, C11.2, C12.2, C13.2, C14.2, C15.2, C16.1, C17.1, C18.2, C19.2, C20.2, C21.2, C22.2, C23.2, C24.2, C25.2, H1.1, H2.1, H3.1, H4.1, J1.5, J2.1 (-), J3.A1 (GND), J3.A12 (GND), J3.B1 (GND), J3.B12 (GND), J4.1, J5.6 (GND), J5.8 (GND), J9.4, J10.4, J11.2, J13.2, J14.1, J14.3, R1.2, R2.2, R3.2, R5.2, R6.2, R7.1, R10.1, R14.2, R15.2, R16.2, R17.2, R18.2, R19.2, R29.1, R30.1, SW1.4, SW2.4, SW3.4, SW4.4, SW5.4, SW6.4, SW7.4, SW8.4, SW9.4, U1.6 (GND), U2.3 (GND), U3.4, U3.5, U3.6, U3.7, U3.8, U4.2 (GND), U4.8 (S), U5.2 (GND), U6.2 (GND), U7.1 (GND), U7.40 (GND), U7.41 (GND), U8.6 (GND), U9.6 (GND)
I2C_SCL: J11.3, R13.2, U2.5 (SCL), U7.20 (IO12)
I2C_SDA: J11.4, R12.2, U2.6 (SDA), U7.19 (IO11)
J5_DIR: R1.1, U1.1 (DIR), U7.21 (IO13)
J5_PWM: R2.1, U1.12 (PWM), U7.10 (IO17)
J5_QUAD_A: J1.4, U7.11 (IO18)
J5_QUAD_B: J1.3, U7.12 (IO8)
J34_L_DIR: R14.1, U7.8 (IO15), U8.1 (DIR)
J34_L_PWM: R15.1, U7.9 (IO16), U8.12 (PWM)
J34_R_DIR: R17.1, U7.36 (RXD0), U9.1 (DIR)
J34_R_PWM: R18.1, U7.37 (TXD0), U9.12 (PWM)
M5_LS_CLOSED: J13.1, R21.2, U7.18 (IO10)
unnamed: C8.1, R8.1, R9.2
unnamed: D1.1 (K), R10.2
unnamed: D2.1 (K), J6.5
unnamed: D3.1 (K), R29.2
unnamed: D4.1 (K), R30.2
unnamed: F1.2, J2.2 (+)
unnamed: C7.1, J3.S1 (SHIELD)
unnamed: J5.9 (G_L-), R7.2
unnamed: J7.2 (+), U8.7 (OUT2)
unnamed: J7.1 (-), U8.5 (OUT1)
unnamed: J8.2 (+), U9.7 (OUT2)
unnamed: J8.1 (-), U9.5 (OUT1)
unnamed: R33.2, U1.9 (~CS)
unnamed: R3.1, U1.11 (~EN(DIS))
unnamed: R31.2, U8.9 (~CS)
unnamed: R16.1, U8.11 (~EN(DIS))
unnamed: R32.2, U9.9 (~CS)
unnamed: R19.1, U9.11 (~EN(DIS))
PB_J3_FWD: R23.2, SW4.1, SW4.2, U7.35 (IO42)
PB_J3_REV: R22.2, SW3.1, SW3.2, U7.34 (IO41)
PB_J4_FWD: R25.2, SW6.1, SW6.2, U7.38 (IO2)
PB_J4_REV: R24.2, SW5.1, SW5.2, U7.31 (IO38)
PB_J5_CLOSE: R28.2, SW9.1, SW9.2, U7.32 (IO39)
PB_J5_OPEN: R27.2, SW8.1, SW8.2, U7.39 (IO1)
PB_J34_CALIB: R26.2, SW7.1, SW7.2, U7.33 (IO40)
SPI_CS_ENC_L: J9.6, U7.7 (IO7)
SPI_CS_ENC_R: J10.6, U7.22 (IO14)
SPI_MISO: J9.5, J10.5, U7.23 (IO21)
SPI_MOSI: J9.3, J10.3, U7.25 (IO48)
SPI_SCK: J9.2, J10.2, U7.24 (IO47)
USB_N: J3.A7 (D-), J3.B7 (D-), U3.3, U7.13 (IO19-USB_N)
USB_P: J3.A6 (D+), J3.B6 (D+), U3.2, U7.14 (IO20-USB-P)

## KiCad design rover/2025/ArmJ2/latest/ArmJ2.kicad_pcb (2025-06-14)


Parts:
C1, C3, C4, C6, C7, C9, C11, C14: 100nF; C_0805_2012Metric_Pad1.18x1.45mm_HandSolder
C2: 22uF; C_0805_2012Metric_Pad1.18x1.45mm_HandSolder
C5: 1uF; C_0805_2012Metric_Pad1.18x1.45mm_HandSolder
C8, C10, C12, C13, C15, C16: 10uF; C_0805_2012Metric_Pad1.18x1.45mm_HandSolder
D1: G; LED_0805_2012Metric_Pad1.15x1.40mm_HandSolder
D2, D3, D5: B; LED_0805_2012Metric_Pad1.15x1.40mm_HandSolder
D4: 40V; D_SMA
F1: FuseHolder; FUSE_3568-20
G1, G6: PHR-3
G3: JUMPER 2PINS (QPC02SXGN-RC)
G4: PHR-2
G8: PHR-6
H1, H2, H3, H4: MountingHole_Pad; MountingHole_3.2mm_M3_DIN965_Pad_TopBottom
J1: USB_C_USB4105-GF-A; USB_C_Receptacle_GCT_USB4105-xx-A_16P_TopMnt_Horizontal
J2: XT30PW-F; AMASS_XT30PW-F_1x02_P2.50mm_Horizontal; PARTREV 1.2
J3, J4: Eth-Horiz; Ethernet_Horizontal
J5: Conn_01x03; JST_PH_S3B-PH-K_1x03_P2.00mm_Horizontal
J6: Conn_01x02; JST_PH_S2B-PH-K_1x02_P2.00mm_Horizontal
J8: Conn_01x03; JST_PH_B3B-PH-K_1x03_P2.00mm_Vertical
J9: Conn_01x06; JST_PH_B6B-PH-K_1x06_P2.00mm_Vertical
J10: Jumper PWR; PinHeader_2x03_P2.54mm_Vertical
R1, R2, R4, R5, R6, R11: 5.1k; R_0805_2012Metric_Pad1.20x1.40mm_HandSolder
R3, R7, R8: 10k; R_0805_2012Metric_Pad1.20x1.40mm_HandSolder
R10: 120; R_0805_2012Metric_Pad1.20x1.40mm_HandSolder
SW1, SW2, SW3, SW4: SW-PTS815SJM250SMTRLFS; SW-PTS815 SJM250SMTRLFS
U1: TVS-SMDB03CE3; SOIC-8_3.9x4.9mm_P1.27mm
U2: ESP32-S3-WROVER; ESP32-S3-WROOM-1U
U3: XT60PM-F; AMASS_XT60PW-F_1x02_P7.20mm_Horizontal
U4: XT60PW-M; AMASS_XT60PW-M_1x02_P7.20mm_Horizontal
U5: LDO-TLV74033PDBVR; SOT-23-5_HandSoldering
U6, U7: SN65HVD232; SOIC-8_3.9x4.9mm_P1.27mm; PARTREV 4
U8: LDO-LM7805MPX/NOPB; SOT-223-3_TabPin2

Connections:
+3.3V: C2.1, C3.1, C8.1, C9.1, C10.1, C11.1, C13.1, J8.2, R3.1, R4.1, R7.1, R8.1, U2.2 (3V3), U5.5 (OUTPUT), U6.3 (VCC), U7.3 (VCC)
+5V: C6.1, C12.1, C16.1, J9.1, J10.6, R11.1, U5.1 (INPUT), U5.3 (EN), U8.3 (OUTPUT)
+5V_USB: D4.2 (A), J1.A4 (VBUS), J1.A9 (VBUS), J1.B4 (VBUS), J1.B9 (VBUS), U1.1
+24V: F1.2, U3.2 (+), U4.2 (+)
+24V_Logic: J3.5, J3.7, J4.5, J4.7, J10.3
+24V_safe: F1.1, J2.2 (+), J10.1
CAN+: J3.1 (CANH), J4.1 (CANH), U6.7 (CANH)
CAN-: J3.2 (CANL), J4.2 (CANL), U6.6 (CANL)
CAN_M+: J6.1, R10.1, U7.7 (CANH)
CAN_M-: J6.2, R10.2, U7.6 (CANL)
CUI_CS: J9.6, U2.38 (IO2)
CUI_MISO: J9.5, U2.20 (IO12)
CUI_MOSI: J9.3, U2.21 (IO13)
CUI_SCLK: J9.2, U2.22 (IO14)
EN_PB: C1.2, C5.1, R3.2, SW1.4, U2.3 (EN)
Enco_Pot: J8.1, U2.39 (IO1)
GND: C1.1, C2.2, C3.2, C4.1, C5.2, C6.2, C7.1, C8.2, C9.2, C10.2, C11.2, C12.2, C13.2, C14.1, C15.2, C16.2, D1.1 (K), D2.1 (K), D3.1 (K), D5.1 (K), H1.1, H2.1, H3.1, H4.1, J1.A1 (GND), J1.A12 (GND), J1.B1 (GND), J1.B12 (GND), J2.1 (-), J3.6, J3.8, J4.6, J4.8, J5.1, J8.3, J9.4, R1.2, R2.2, SW1.1, SW1.2, SW2.1, SW2.2, SW3.1, SW3.2, SW4.1, SW4.2, U1.5, U1.6, U1.7, U1.8, U2.1 (GND), U2.40 (GND), U2.41 (GND), U3.1 (-), U4.1 (-), U5.2 (GND), U6.2 (GND), U6.8 (S), U7.2 (GND), U7.8 (S), U8.2 (GND)
GPIO_0: C4.2, SW2.4, U2.27 (IO0-BOOT)
Jog+: C14.2, R7.2, SW3.4, U2.19 (IO11)
Jog-: C7.2, R8.2, SW4.4, U2.18 (IO10)
LED_BUILTIN: R5.1, U2.17 (IO9)
LED_ERR: R6.1, U2.12 (IO8)
unnamed: D1.2 (A), R4.2
unnamed: D2.2 (A), R5.2
unnamed: D3.2 (A), R6.2
unnamed: D4.1 (K), J10.5
unnamed: D5.2 (A), R11.2
unnamed: J1.A5 (CC1), R1.1
unnamed: J1.B5 (CC2), R2.1
unnamed: C15.1, J10.2, J10.4, U8.1 (INPUT)
RXC: U2.25 (IO48), U6.4 (RXD)
RXC_M: U2.4 (IO4), U7.4 (RXD)
RX_M: J5.2, U2.6 (IO6)
TXC: U2.24 (IO47), U6.1 (TXD)
TXC_M: U2.5 (IO5), U7.1 (TXD)
TX_M: J5.3, U2.7 (IO7)
USB_N: J1.A7 (D-), J1.B7 (D-), U1.2, U2.13 (IO19-USB_N)
USB_P: J1.A6 (D+), J1.B6 (D+), U1.3, U2.14 (IO20-USB-P)

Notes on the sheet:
ESP32
Data Connector IN (RJ45)
OUT
Mounting Holes
Encodeur SPI
Power Connectors (XT60)
JST Connector Motor Comm. UART
Main CAN
Motor CAN
There are 3 different communications: -Main CAN, for Rover to Drive comm. (CANH/CANL, TXC/RXC) -Motor comm. over CAN (CANH_M/CANL_M, TXC_M/RXC_M) -Motor comm. over UART (TX_M, RX_M)
ESP LDO
Alimentation Motor
Boot ESP32 Button
Jog Buttons
Enable ESP32 Button
CAN Tranceivers
Data Connector OUT (RJ45)
USB C
LEDs
Encondeur POT
JST Connector Motor Comm. CAN

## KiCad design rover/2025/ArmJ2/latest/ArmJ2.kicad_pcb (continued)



Board: 4 copper layers, 70.0 x 53.0 mm, 57 parts (27 on the bottom side), 38 nets.

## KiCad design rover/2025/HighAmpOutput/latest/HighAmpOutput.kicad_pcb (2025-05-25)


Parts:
G1: PHR-2
G2: CFM-4020V-280-275
H1, H2, H3, H4: MountingHole_Pad; MountingHole_3.2mm_M3_DIN965_Pad_TopBottom

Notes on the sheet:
This is a component
xt60_DDB
xt60_Sélecteur
Ce PCB sert à distribuer l'alimentation au reste des PCB du rover. Le DDB et le sélecteur sont directement aliementer et les autres PCB sont sur du 24v controler. Les autres PCB sont alimenter lorsque le sélecteur envoie un signal au HighAmpOutput.
EC5
TODO: - Add external componenents
JST
Add parts like connectors, crimps or other which needs to be ordered with the PCB. Don't forget to check the "remove from board" option
VN7004
xt60 x 6
FAN
Off board parts to order
Mechanical parts
This is a data wire
- Layer count: 4 - Stackup nb: JLC041622-3313
PCB Decription
Board block schematic
This is a High Current Wire
PCB Order settings


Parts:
C1: 1n; C_0805_2012Metric_Pad1.18x1.45mm_HandSolder
D1, D2: R; LED_0805_2012Metric_Pad1.15x1.40mm_HandSolder
J1: Conn_01x03; JST_PH_B3B-PH-K_1x03_P2.00mm_Vertical
J2: JST-PH-B2B; JST_PH_B2B-PH-K_1x02_P2.00mm_Vertical
R1, R4, R6: 15k; R_0805_2012Metric_Pad1.20x1.40mm_HandSolder
R2: 100k; R_0805_2012Metric_Pad1.20x1.40mm_HandSolder
R3, R5: 1K; R_0805_2012Metric_Pad1.20x1.40mm_HandSolder
U1: EC5_Connector; EC5
U2: HSS-VN7004SLHTR; OCTAPACK_VN7004_STM-M
U3, U4, U5, U6, U7, U8: XT60-F; AMASS_XT60-F_1x02_P7.20mm_Vertical
U11, U12: XT60PM-F; AMASS_XT60PW-F_1x02_P7.20mm_Horizontal

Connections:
+24V: J1.1, R5.1, U2.1 (OUT), U2.2 (OUT), U2.3 (OUT), U3.2 (+), U4.2 (+), U5.2 (+), U6.2 (+), U7.2 (+), U8.2 (+)
+24V_I: R3.1, U1.1 (Vout+), U2.8 (Vcc), U11.2 (+), U12.2 (+)
GND: C1.2, D1.1 (K), D2.1 (K), J1.3, R1.2, R2.2, R4.2, U1.2 (Vout-), U2.7 (GND), U3.1 (-), U4.1 (-), U5.1 (-), U6.1 (-), U7.1 (-), U8.1 (-), U11.1 (-), U12.1 (-)
unnamed: D1.2 (A), R3.2
unnamed: D2.2 (A), R5.2
unnamed: J2.1, R6.1
unnamed: C1.1, J2.2
unnamed: R4.1, U2.5 (CS)
unnamed: R1.1, U2.6 (FR_DIAG)
unnamed: R2.1, R6.2, U2.4 (INPUT)

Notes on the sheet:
Légend: -+24V_I: 24v non-contrôler -+24v: 24v contrôler
Connecteur XT60 non-contrôler
Connecteur contrôler par le VN7004
Connecteur De voltage D'entrée (Connecteur EC5)
Circuit de contrôle avec le VN7004


Board: 4 copper layers, 78.0 x 39.0 mm, 25 parts (0 on the bottom side), 10 nets.

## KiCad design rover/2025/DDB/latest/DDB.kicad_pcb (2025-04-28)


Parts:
C1: 1uF; C_0805_2012Metric_Pad1.18x1.45mm_HandSolder
C2: 22uF; C_0805_2012Metric_Pad1.18x1.45mm_HandSolder
C3, C4, C5, C7, C8: 100nF; C_0805_2012Metric_Pad1.18x1.45mm_HandSolder
C6, C9, C10, C11, C12, C17, C18, C19, C20, C23, C24, C25: 10uF; C_0805_2012Metric_Pad1.18x1.45mm_HandSolder
D1, D2: R; D_0805_2012Metric_Pad1.15x1.40mm_HandSolder
D3: G; D_0805_2012Metric_Pad1.15x1.40mm_HandSolder
D4, D5: B; D_0805_2012Metric_Pad1.15x1.40mm_HandSolder
F1: 20A; FUSE_3568-20
F2, F3, F4, F5, F6, F7, F8, F10, F11: 3A; FUSE_3568-20
G1, G2, G3, G4, G5, G6, G7, G8, G9: 3A Fuse
G10: 20A Fuse
H6, H7: MountingHole_Pad; MountingHole_3.2mm_M3_DIN965_Pad_TopBottom
J1: USB_C_USB4145-GCT; USB4145_GCT
J2, J4: ETH-RJHSE508104
J3: TerminalBlock; TerminalBlock-4_P5.00mm-691137710004; PART-NUMBER 691137710004
J8: XT30PW-F; AMASS_XT30PW-F_1x02_P2.50mm_Horizontal; PARTREV 1.2
JP1: SolderJumper_3_Open; PinHeader_1x03_P2.54mm_Vertical
R1: 10k; R_0805_2012Metric_Pad1.20x1.40mm_HandSolder
R2, R3, R5, R17, R18, R21, R22, R23, R24, R25, R26: 4.7k; R_0805_2012Metric_Pad1.20x1.40mm_HandSolder
R4, R6, R7, R8: 1k; R_0805_2012Metric_Pad1.20x1.40mm_HandSolder
R9, R10, R13, R14, R16, R20, R29, R30, R33, R34, R35, R36, R37, R38, R39, R40, R41, R42, R43, R44, R45, R46, R47, R48, R49, R50, R51: 15k; R_0805_2012Metric_Pad1.20x1.40mm_HandSolder
R11, R12, R15, R19, R27, R28, R31, R32: 100k; R_0805_2012Metric_Pad1.20x1.40mm_HandSolder
SW1, SW2: TS09-63-25-WT-160-SMT-TR; SW_DIP_SPSTx01_Slide_6.7x4.1mm_W8.61mm_P2.54mm_LowProfile
U1: ESP32-S3-WROVER; ESP32-S3-WROOM-1U
U2: TVS-SMDB03CE3; SOIC-8_3.9x4.9mm_P1.27mm
U3: SN65HVD232; SOIC-8_3.9x4.9mm_P1.27mm; PARTREV 4
U4: TLE4284DV33ATMA1; TO-252-2
U5: XT60PW-M; AMASS_XT60PW-M_1x02_P7.20mm_Horizontal
U6, U7, U8, U9, U10, U11, U12, U13, U14: HSS-VN7004SLHTR; OCTAPACK_VN7004_STM-M

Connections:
+3.3V: C2.1, C3.1, C6.1, C7.1, C10.1, R1.1, R6.1, U1.2 (3V3), U3.3 (VCC), U4.2 (OUTPUT)
+5V: J1.A4 (VBUS), J1.A9 (VBUS), J1.B4 (VBUS), J1.B9 (VBUS), JP1.3 (B), U2.1
+24V_L: C11.1, C12.1, C17.1, C18.1, C19.1, C20.1, C23.1, C24.1, C25.1, F2.2, F3.2, F4.2, F5.2, F6.2, F7.2, F8.2, F10.2, F11.2, JP1.1 (A), R4.1, R5.1, U6.1 (OUT), U6.2 (OUT), U6.3 (OUT)
+24V_OUT_1: J2.1_5 (Vcc), J2.1_7 (Vcc), J2.1_10 (G_L+), U7.1 (OUT), U7.2 (OUT), U7.3 (OUT)
+24V_OUT_2: J2.2_5 (Vcc), J2.2_7 (Vcc), J2.2_10 (G_L+), U8.1 (OUT), U8.2 (OUT), U8.3 (OUT)
+24V_OUT_3: J2.3_5 (Vcc), J2.3_7 (Vcc), J2.3_10 (G_L+), U9.1 (OUT), U9.2 (OUT), U9.3 (OUT)
+24V_OUT_4: J2.4_5 (Vcc), J2.4_7 (Vcc), J2.4_10 (G_L+), U10.1 (OUT), U10.2 (OUT), U10.3 (OUT)
+24V_OUT_5: J4.1_5 (Vcc), J4.1_7 (Vcc), J4.1_10 (G_L+), U13.1 (OUT), U13.2 (OUT), U13.3 (OUT)
+24V_OUT_6: J4.2_5 (Vcc), J4.2_7 (Vcc), J4.2_10 (G_L+), U14.1 (OUT), U14.2 (OUT), U14.3 (OUT)
+24V_OUT_7: J4.3_5 (Vcc), J4.3_7 (Vcc), J4.3_10 (G_L+), U11.1 (OUT), U11.2 (OUT), U11.3 (OUT)
+24V_OUT_8: J4.4_5 (Vcc), J4.4_7 (Vcc), J4.4_10 (G_L+), U12.1 (OUT), U12.2 (OUT), U12.3 (OUT)
/BOOT: C4.2, SW1.2, U1.27 (IO0-BOOT)
/CAN_LED: R7.1, U1.39 (IO1)
/CAN_N: J2.1_2 (CANL), J2.2_2 (CANL), J2.3_2 (CANL), J2.4_2 (CANL), J3.3, U3.6 (CANL)
/CAN_P: J2.1_1 (CANH), J2.2_1 (CANH), J2.3_1 (CANH), J2.4_1 (CANH), J3.4, U3.7 (CANH)
/CC1: J1.A5 (CC1), R2.1
/CC2: J1.B5 (CC2), R3.1
/EN_PB: C1.1, C5.2, R1.2, SW2.2, U1.3 (EN)
/LED_BUILDIN: R8.1, U1.38 (IO2)
/LOW_PW_EN: J3.1, R43.1
/RXC: U1.24 (IO47), U3.1 (TXD)
/SIGN_OUT_24_1: R44.1, U1.23 (IO21)
/SIGN_OUT_24_2: R45.1, U1.21 (IO13)
/SIGN_OUT_24_3: R47.1, U1.19 (IO11)
/SIGN_OUT_24_4: R48.1, U1.4 (IO4)
/SIGN_OUT_24_5: R46.1, U1.6 (IO6)
/SIGN_OUT_24_6: R49.1, U1.8 (IO15)
/SIGN_OUT_24_7: R50.1, U1.10 (IO17)
/SIGN_OUT_24_8: R51.1, U1.12 (IO8)
/TXC: U1.25 (IO48), U3.4 (RXD)
/USB_N: J1.A7 (D-), J1.B7 (D-), U1.13 (IO19-USB_N), U2.2
/USB_P: J1.A6 (D+), J1.B6 (D+), U1.14 (IO20-USB-P), U2.3
GND: C1.2, C2.2, C3.2, C4.1, C5.1, C6.2, C7.2, C8.2, C9.2, C10.2, C11.2, C12.2, C17.2, C18.2, C19.2, C20.2, C23.2, C24.2, C25.2, D1.1 (K), D2.1 (K), D3.1 (K), D4.1 (K), D5.1 (K), H6.1, H7.1, J1.A1 (GND), J1.A12 (GND), J1.B1 (GND), J1.B12 (GND), J2.1_6 (GND), J2.1_8 (GND), J2.2_6 (GND), J2.2_8 (GND), J2.3_6 (GND), J2.3_8 (GND), J2.4_6 (GND), J2.4_8 (GND), J3.2, J4.1_6 (GND), J4.1_8 (GND), J4.2_6 (GND), J4.2_8 (GND), J4.3_6 (GND), J4.3_8 (GND), J4.4_6 (GND), J4.4_8 (GND), J8.1 (-), R2.2, R3.2, R9.2, R10.2, R11.2, R12.2, R13.2, R14.2, R15.2, R16.2, R17.1, R18.1, R19.2, R20.2, R21.1, R22.1, R23.1, R24.1, R25.1, R26.1, R27.2, R28.2, R29.2, R30.2, R31.2, R32.2, R33.2, R34.2, R35.2, R36.2, R37.2, R38.2, R39.2, R40.2, R41.2, R42.2, SW1.1, SW2.1, U1.1 (GND), U1.40 (GND), U1.41 (GND), U2.5, U2.6, U2.7, U2.8, U3.2 (GND), U3.8 (S), U4.1 (GND), U5.1 (-), U6.7 (GND), U7.7 (GND), U8.7 (GND), U9.7 (GND), U10.7 (GND), U11.7 (GND), U12.7 (GND), U13.7 (GND), U14.7 (GND)
unnamed: D1.2 (A), R4.2
unnamed: D2.2 (A), R5.2
unnamed: D3.2 (A), R6.2
unnamed: D4.2 (A), R7.2
unnamed: D5.2 (A), R8.2
unnamed: J2.1_9 (G_L-), R17.2
unnamed: J2.2_9 (G_L-), R18.2
unnamed: J2.3_9 (G_L-), R21.2
unnamed: J2.4_9 (G_L-), R22.2
unnamed: J4.1_9 (G_L-), R23.2
unnamed: J4.2_9 (G_L-), R24.2
unnamed: J4.3_9 (G_L-), R25.2
unnamed: J4.4_9 (G_L-), R26.2
unnamed: F6.1, J8.2 (+)
unnamed: C8.1, C9.1, JP1.2 (C), U4.3 (INPUT)
unnamed: F1.2, U5.2 (+)
unnamed: R9.1, U6.5 (CS)
unnamed: R10.1, U6.6 (FR_DIAG)
unnamed: R43.2, U6.4 (INPUT)
unnamed: F1.1, U6.8 (Vcc)
unnamed: R13.1, U7.5 (CS)
unnamed: R35.1, U7.6 (FR_DIAG)
unnamed: R11.1, R44.2, U7.4 (INPUT)
unnamed: F2.1, U7.8 (Vcc)
unnamed: R14.1, U8.5 (CS)
unnamed: R38.1, U8.6 (FR_DIAG)
unnamed: R12.1, R45.2, U8.4 (INPUT)
unnamed: F3.1, U8.8 (Vcc)
unnamed: R16.1, U9.5 (CS)
unnamed: R41.1, U9.6 (FR_DIAG)
unnamed: R15.1, R47.2, U9.4 (INPUT)
unnamed: F4.1, U9.8 (Vcc)
unnamed: R20.1, U10.5 (CS)
unnamed: R36.1, U10.6 (FR_DIAG)
unnamed: R19.1, R48.2, U10.4 (INPUT)
unnamed: F5.1, U10.8 (Vcc)
unnamed: R29.1, U11.5 (CS)
unnamed: R37.1, U11.6 (FR_DIAG)
unnamed: R27.1, R50.2, U11.4 (INPUT)
unnamed: F7.1, U11.8 (Vcc)
unnamed: R30.1, U12.5 (CS)
unnamed: R40.1, U12.6 (FR_DIAG)
unnamed: R28.1, R51.2, U12.4 (INPUT)
unnamed: F8.1, U12.8 (Vcc)
unnamed: R33.1, U13.5 (CS)
unnamed: R39.1, U13.6 (FR_DIAG)
unnamed: R31.1, R46.2, U13.4 (INPUT)
unnamed: F10.1, U13.8 (Vcc)
unnamed: R34.1, U14.5 (CS)
unnamed: R42.1, U14.6 (FR_DIAG)
unnamed: R32.1, R49.2, U14.4 (INPUT)
unnamed: F11.1, U14.8 (Vcc)

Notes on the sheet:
Boot ESP32 Button
Mounting holes
Off Board Parts
Data Input
ESP32
USB C
24V Output
CAN Transceiver
24V HSS
Power Input
Enable ESP32 Button
Power LED
LDO 3.3V
Optional Condos
PC Power (Always On)



Board: 4 copper layers, 152.8 x 53.5 mm, 109 parts (40 on the bottom side), 85 nets.

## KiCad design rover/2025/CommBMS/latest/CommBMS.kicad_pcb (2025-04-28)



Board: 4 copper layers, 50.5 x 50.0 mm, 37 parts (6 on the bottom side), 31 nets.

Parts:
C1, C2, C4, C6, C10: 100nF; C_0805_2012Metric_Pad1.18x1.45mm_HandSolder
C3, C5, C7, C8, C9: 10uF; C_0805_2012Metric_Pad1.18x1.45mm_HandSolder
C11: 1uF; C_0805_2012Metric_Pad1.18x1.45mm_HandSolder
C12: 1n; C_0805_2012Metric_Pad1.18x1.45mm_HandSolder
D1: R; LED_0805_2012Metric_Pad1.15x1.40mm_HandSolder
D2: G; LED_0805_2012Metric_Pad1.15x1.40mm_HandSolder
D3: CVJ10F30; Diode_schottky-CVJ10F30
H1, H2, H3: MountingHole_Pad; MountingHole_3.2mm_M3_DIN965_Pad_TopBottom
J1, J2: Eth-Horiz-54601-908WPLF; Ethernet_Horizontal
J3: USB_C_USB4105-GF-A; USB_C_Receptacle_GCT_USB4105-xx-A_16P_TopMnt_Horizontal
J4: CONN-MOLEX_8PIN-39301080
R1, R2: 1k; R_0805_2012Metric_Pad1.20x1.40mm_HandSolder
R3, R4: 5k1; R_0805_2012Metric_Pad1.20x1.40mm_HandSolder
R5, R6: 0; R_0603_1608Metric_Pad0.98x0.95mm_HandSolder
R7: 10k; R_0805_2012Metric_Pad1.20x1.40mm_HandSolder
SW1, SW2: TS09-63-25-WT-160-SMT-TR; SW-PTS815 SJM250SMTRLFS
U1: SN65HVD232Q; SOIC-8_3.9x4.9mm_P1.27mm
U2: TVS; SOIC-8_3.9x4.9mm_P1.27mm
U3: LDO-LM7805MPX/NOPB; TO-263-3_TabPin2
U4: SP3485EN; SOIC-8_3.9x4.9mm_P1.27mm
U5: ESP32-S3-WROOM-1; ESP32-S3-WROOM-1U
U7: AXP1T34; SOT-353_SC-70-5

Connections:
+3.3V: C3.1, C4.1, C5.1, C6.1, C8.1, C9.1, C10.1, R2.2, R7.1, U1.3 (VCC), U3.2 (OUTPUT), U4.8 (VCC), U5.2 (3V3), U7.5 (Vcco)
+5V_BMS: J4.5, R5.1
+5V_USB: D3.3, J3.A4 (VBUS), J3.A9 (VBUS), J3.B4 (VBUS), J3.B9 (VBUS), U2.3
+24V_ETH: D3.1, J1.5, J1.7, J2.5, J2.7
BMS_A: J4.1, U4.6 (A)
BMS_B: J4.2, U4.7 (B)
CANH: J1.1 (CANH), J2.1 (CANH), U1.7 (CANH)
CANL: J1.2 (CANL), J2.2 (CANL), U1.6 (CANL)
DE: U4.3 (DE), U5.20 (IO12)
DIN2: J4.8, U5.10 (IO17)
EN_PB: C1.2, C11.1, R7.2, SW1.4, U5.3 (EN)
GND: C1.1, C2.1, C3.2, C4.2, C5.2, C6.2, C7.2, C8.2, C9.2, C10.2, C11.2, C12.2, D1.1 (K), D2.1 (K), H1.1, H2.1, H3.1, J1.6, J1.8, J2.6, J2.8, J3.A1 (GND), J3.A12 (GND), J3.B1 (GND), J3.B12 (GND), J4.7, R3.2, R4.2, SW1.1, SW1.2, SW2.1, SW2.2, U1.2 (GND), U1.8 (S), U2.4, U2.5, U2.6, U2.7, U2.8, U3.1 (GND), U4.5 (GND), U5.1 (GND), U5.40 (GND), U5.41 (GND), U7.3 (GND)
GPIO_0: C2.2, SW2.4, U5.27 (IO0-BOOT)
LED_BUILDIN: R1.2, U5.39 (IO1)
unnamed: D1.2 (A), R1.1
unnamed: D2.2 (A), R2.1
unnamed: J3.A5 (CC1), R3.1
unnamed: J3.B5 (CC2), R4.1
unnamed: C12.1, J3.S1 (SHIELD)
unnamed: C7.1, D3.4, D3.5, U3.3 (INPUT)
unnamed: R6.2, U7.2 (INPUT)
unnamed: R5.2, U7.1 (Vcci)
PWM_3V: U5.11 (IO18), U7.4 (OUTPUT)
PWM_5V: J4.6, R6.1
RE: U4.2 (RE), U5.19 (IO11)
RXB: U4.1 (RXD), U5.18 (IO10)
RXC: U1.4 (RXD), U5.25 (IO48)
TXB: U4.4 (TXD), U5.17 (IO9)
TXC: U1.1 (TXD), U5.24 (IO47)
USB_N: J3.A7 (D-), J3.B7 (D-), U2.1, U5.13 (IO19-USB_N)
USB_P: J3.A6 (D+), J3.B6 (D+), U2.2, U5.14 (IO20-USB-P)

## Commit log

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2024-03-27 Final V1 version, ready to order
    [gripper_2024-B_Cu.gbl, gripper_2024-B_Mask.gbs, gripper_2024-B_Paste.gbp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]
2024-03-30 New Can bus termination PCB
    [2024-03-24.ods, 54601-908WPLF.step, AJP92A8813.stp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]
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2024-04-03 rovus esp32-s3 devkit + gps module
    [54601-908WPLF.step, Beitian BN-880 GPS and Compas.step, ESP32-DevKit.stp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]
2024-04-03 Fix wrong file name
    [esp32_rover_devkit.csv, esp32_rover_devkit.ods]
2024-04-03 Shield Drive Moteur DC
    [3555-2.step, BOM - Shield Drive Moteur DC.xlsx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]
2024-04-08 Auto stash before merge of "main" and "origin/main"
    [esp32_rover_devkit.ods]
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2024-04-18 fix terminaison
    [1790335.step, 3568-20.step, 54601-908WPLF.step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]
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2024-04-20 pcb j0 + j1
    [54601-908WPLF.step, A-2014-2-4-N-T-R.step, Beitian BN-880 GPS and Compas.step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]
2024-04-21 final j0 + j1 drive
    [arm_drive.kicad_pcb]
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2024-04-24 Updated wrong footprint in rocker splitter
    [rocker_splitter.kicad_pcb]
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2024-05-16 new driver to replace talon srx
    [54601-908WPLF.step, A-2014-2-4-N-T-R.step, Beitian BN-880 GPS and Compas.step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]
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2024-07-01 redone arm drive with 24V input + fuse
    [3568-20.step, arm_drive.kicad_pcb, arm_drive.kicad_sch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]
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2024-07-01 fuse j2 drive + 24v ldo
    [3568-20.step, arm_drive_j2.csv, arm_drive_j2.kicad_pcb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]
2024-07-02 RockerSplitter current rating adjustement
    [rocket_splitter_v2.kicad_pcb, rocket_splitter_v2.kicad_sch]
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2024-07-02 Drive27A Thermal design validation
    [drive_27A.kicad_pcb]
2024-07-03 ArmDrive J0+J1 Thermal design validation
    [arm_drive.kicad_pcb]
2024-07-03 ArmDrive J2 Thermal design validation
    [arm_drive_j2.kicad_pcb]
2024-07-07 arm drive JL done
    [3568-20.step, 54601-908WPLF.step, A-2014-2-4-N-T-R.step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]
2024-07-07 arm drive JL export files
    [REV0.csv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]
2024-07-08 pcb science in progress
    [3568-20.step, 54601-908WPLF.step, A-2014-2-4-N-T-R.step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]
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2024-07-09 science: layout done missing silk layer
    [science_module.kicad_pcb, science_module.kicad_sch]
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2024-07-19 rev3 rockersplitter in progress
    [3550-2.step, blade_fuse.step, rocket_splitter_v2.kicad_pcb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]
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2024-07-19 added fuse 3d on j3,4,5
    [Fusibile Lama MINI Type 1.stp, Fusibile Lama MINI Type 2.stp, arm_drive_j3_4_5.kicad_pcb]
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2024-07-25 Ajout de la V1 du PCB Antenna dans .../antenna
    [24V-5V.kicad_sch, 54601-908WPLF.step, A-2014-2-4-N-T-R.step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]
2024-07-26 fix gpio39 on j3_4_5
    [arm_drive_j3_4_5.kicad_pcb, arm_drive_j3_4_5.kicad_sch]
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2024-10-24 Fichier de fab Drive_27A
    Génération des fichier de fabrication pour la Drive_27A
    [drive_27A-B_Cu.gbl, drive_27A-B_Mask.gbs, drive_27A-B_Paste.gbp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]
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2024-10-24 Supression de fichiers du .gitignore
    Fichier de fabrication
    Fichiers de Backups
    Fichiers .DS_Store
    [Shield Drive Moteur DC-B_Cu.gbl, Shield Drive Moteur DC-B_Mask.gbs, Shield Drive Moteur DC-B_Paste.gbp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]
2024-10-25 Add file of the moustache
    [Projet moustache.kicad_pcb, Projet moustache.kicad_sch]
2024-11-06 V2.1 du BNOV
    version préliminaire du BNOV2.
    [BNO_BREAKOUT.kicad_pcb, BNO_BREAKOUT.kicad_sch]
2024-11-06 Version préliminaire du BNOV
    [BNO_BREAKOUT.kicad_pcb, BNO_BREAKOUT.kicad_sch]
2024-11-28 Edit switched power pins
    [drive_27A.kicad_pcb, drive_27A.kicad_sch]
2024-11-28 Ajout des composants pour la majorité des PCBs
    [3568-20.step, 54601-908WPLF.step, A-2014-2-4-N-T-R.step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]
2024-11-29 Now support 5v to 24v input from eth connector
    [drive_27A.kicad_pcb, drive_27A.kicad_sch]
2024-12-04 Ajout du port USB C
    [USB4105-GF-A.step]
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2024-12-06 Revert "Reorg"
    This reverts commit fb8e8e68ef64dce77992aad18266337ef025036d.
    [1790335.step, 2024-03-24.ods, 3568-20.step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]
2024-12-06 Moved still used project in 2025
    [1790335.step, 24V-5V.kicad_sch, 3550-2.step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]
2024-12-06 New pdb project + lib changes
    [PDB.kicad_pcb, PDB.kicad_sch]
2024-12-10 Modif des PN JLCPCB dans Drive_27A
    [drive_27A.kicad_pcb, drive_27A.kicad_sch]
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2025-01-13 Start of PDB layout
    [DC_DC-DAOKI-MP2315.step, PDB.kicad_pcb, PDB.kicad_sch]
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2025-01-14 Changed name + silkscreen DDB
    [DDB.kicad_pcb, DDB.kicad_sch]
2025-01-15 Modif lib pins
    modification des types de pins pour réduire les erreurs pour que ça soit utile d'utiliser le ERC
    [PDB.kicad_sch]
2025-01-15 add Rover Ethernet Switch + Rover Servo Controller
    [CAN-SW.SchDoc, Connectors_1.SchDoc, Connectors_2.SchDoc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]
2025-01-16 Small 5A regulator pcb
    [regulator.kicad_pcb, regulator.kicad_sch, regulator_5v.kicad_pcb]
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2025-01-22 Update sch and pcb for correct link
    [DDB.kicad_pcb, DDB.kicad_sch]
2025-01-22 Update DDB
    sch and pcb for correct link
    [DDB.kicad_pcb, DDB.kicad_sch]
2025-01-22 Multiple changes to lib + added + fixed pins ERC checks
    [DDB.kicad_pcb, DDB.kicad_sch]
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2025-01-23 Revert "Resistor and Cap 0805"
    This reverts commit 67557315c082f03d933c910415aa55c0264a018f.
2025-01-28 selector schematic done, needs checkup
    [Selector.kicad_pcb, Selector.kicad_sch]
2025-01-29 Reversed switch holder
    [Selector.kicad_sch]
2025-02-03 DDB REV 0 done
    [DDB.kicad_pcb, DDB.kicad_sch, regulator.kicad_pcb]
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2025-02-05 ARM-JL Routing in progress
    [ARM-JL.kicad_pcb, M-RJHSE-X08X-REVT1.STEP, board.kicad_sch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]
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2025-02-06 JST: Change JST 2 pin
    Using the RoverLib One
    [Selector.kicad_pcb, Selector.kicad_sch]
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2025-02-07 Renaming + reorganisation of 2025 project for new standard
    [1790335.step, 2024-03-24.ods, 24V-5V.kicad_sch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]
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2025-02-14 Last touch before order for ARMJL, Regulator and DDB + start of J345
    [ArmJ345.kicad_pcb, ArmJ345.kicad_sch, ArmJL.kicad_pcb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]
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2025-02-17 PCB HighAmpOutput version final
    Devrais être la version final.
    [HighAmpOutput.kicad_pcb, HighAmpOutput.kicad_sch]
2025-02-17 Correction PCB HighAmpOutput
    [HighAmpOutput.kicad_pcb]
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2025-02-19 Selector: Correction symboles
    [Selector.kicad_pcb, Selector.kicad_sch]
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2025-02-19 Rev1 pcb gnss
    Je vais changer le schematic pour qu'il match le template plus tard.
    [GNSS.kicad_pcb, GNSS.kicad_sch]
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2025-02-19 J345 Fix
    [ArmJ345.kicad_pcb, ArmJ345.kicad_sch, HighAmpOutput.kicad_sch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]
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2025-02-19 GNSS Petits changements
    Jacob était à côté de moi quand j'ai ouvert le pcb et il m'a aidé.
    - Skew dans les traces différentielles USB et CAN réglé.
    - Pour le USB, une des deux traces différentielles doit passer à travers des vias afin de swap les deux signaux de côté. Donc, la trace qui ne passe pas par des vias est une épaisseur de board plus longue.
    - Texte pour le connecteur de GNSS flippé pour qu'il soit du bon sens
    - Traces 24V de CAN élargies de 12 mil à 15 mil
    - Ajout d'un condensateur de sortie de 100nF au LDO 35-5 (U3)
    - Changement de la valeur du condensateur de sortie du LDO 5.5-3.3 de 100uF à 10uF
    - Un des connecteurs eth bougé un peu pour laisser plus de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
    [GNSS.kicad_pcb, GNSS.kicad_sch]
2025-02-19 J'avais oublié de re-build les ground planes après mes modifs
    [GNSS.kicad_pcb]
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2025-02-19 Revert "REV GNSS et HAOutput"
    This reverts commit 5d427d660c4e7a301930cd61c736d2448627e1ac.
    [Board.kicad_sch, GNSS.kicad_pcb, HighAmpOutput.kicad_pcb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]
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2025-03-13 Flip RJ45
    Les RJ45 à sont rendus sur l'autre face du PCB pour le rendre moins épais. Les paires différentielles ont été reroute et le transceiver à été bougé pour être plus près.
    Le PCB est toujours pas refait selon le template
    [GNSS.kicad_pcb]
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2025-03-18 Small correction on DDB
    [DDB.kicad_pcb, DDB.kicad_sch]
2025-03-19 Changé position bouton pour que ça rentre dans le casing
    [GNSS.kicad_pcb]
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2025-04-11 fix for rev1
    [ArmJ345.kicad_pcb, canbus.kicad_sch]
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2025-04-18 armj345 fixes
    [ArmJ345.kicad_pcb, drive_j34.kicad_sch, drive_j5.kicad_sch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]
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2025-04-28 DDB: Fixed high current traces width + exported for order REV1
    [DDB-REV1-2025-05-28.csv, DDB.kicad_pcb]
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2025-05-08 Add files via upload
    update servo controller files
    [ESP32.SchDoc]
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2025-05-25 Correction_ERR_PCB_HighAmpOutput
    L'erreur des mauvaises largeur des freins thermique à été corriger (on maintenant: 2 mm). De plus, la description du PCB à été effectuer.
    [HighAmpOutput.kicad_pcb, HighAmpOutput.kicad_sch]
2025-06-14 GNSS power bug fix
    [GNSS.kicad_pcb, GNSS.kicad_sch, L_3.6u_ASPI-6045S-3R6N-T.step]
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2025-07-10 PCB avec bug fixed
    [GasConnBrd.kicad_pcb, Power_Circuit.kicad_sch]
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2026-03-16 Change name of a file that block cloning on windows
    [auxi.kicad_sch]
